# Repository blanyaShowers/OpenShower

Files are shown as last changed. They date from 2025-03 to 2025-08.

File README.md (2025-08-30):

# OpenShower: One Place for Sensations & Sophistication
OpenShower (OS) is a fully open, modular shower system designed to save water and energy — focused on delivering the best shower experience without the need to spend thousands of dollars or modify your bathroom installation. Thanks to its all-in-one, ready-to-use design, you can build it, customize it, and repair it yourself — driven by the vision that owning a premium shower should be as simple as buying a coffee machine.

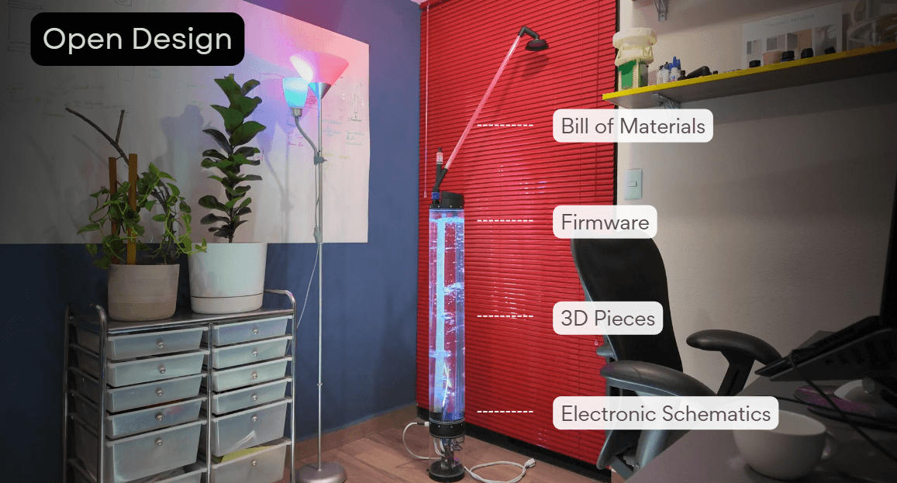
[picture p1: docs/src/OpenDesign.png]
os


OpenShower reinvents the shower experience by eliminating invisible waste and making each session more efficient and sustainable. With a 19-liter tank, it sets a natural water limit that encourages better habits without compromising comfort. The exact amount of water is preheated and delivered instantly, reducing waste during heat-up. Automatic pressure control eliminates the need for manual adjustments, saving time and optimizing water use. The transparent cylinder shows real-time water usage, while the top display reveals insights you’ve likely never seen before.

## Fusion 360:

The 3D model includes only the printable parts and their placement to help you identify each shower component. Acrylic pipes are shown for reference, but they are not intended to be printed.

Colored View: [https://a360.co/467mWWJ](https://a360.co/467mWWJ)

Black View: [https://a360.co/4nfyCwQ](https://a360.co/4nfyCwQ)

## Instructables:

Additional building details based on the YouTube video, plus extra insights about the process.

[https://www.instructables.com/OpenShower-One-Place-for-Sensations-Sophistication/](https://www.instructables.com/OpenShower-One-Place-for-Sensations-Sophistication/)

## Youtube:
The YouTube video walks through the 18 steps to build the model, showing in detail how parts are handled, which tools are used, and extra insights only visible through video.

[https://www.youtube.com/watch?v=CI9o5aMDqA0](https://www.youtube.com/watch?v=CI9o5aMDqA0)

## Kickstarter:
It’s time to break free from monotony, inefficiency, and the lack of innovation and new experiences in our showers. 

[https://www.kickstarter.com/projects/blanya/openshower-waste-ends-here?ref=24dbeq](https://www.kickstarter.com/projects/blanya/openshower-waste-ends-here?ref=24dbeq)

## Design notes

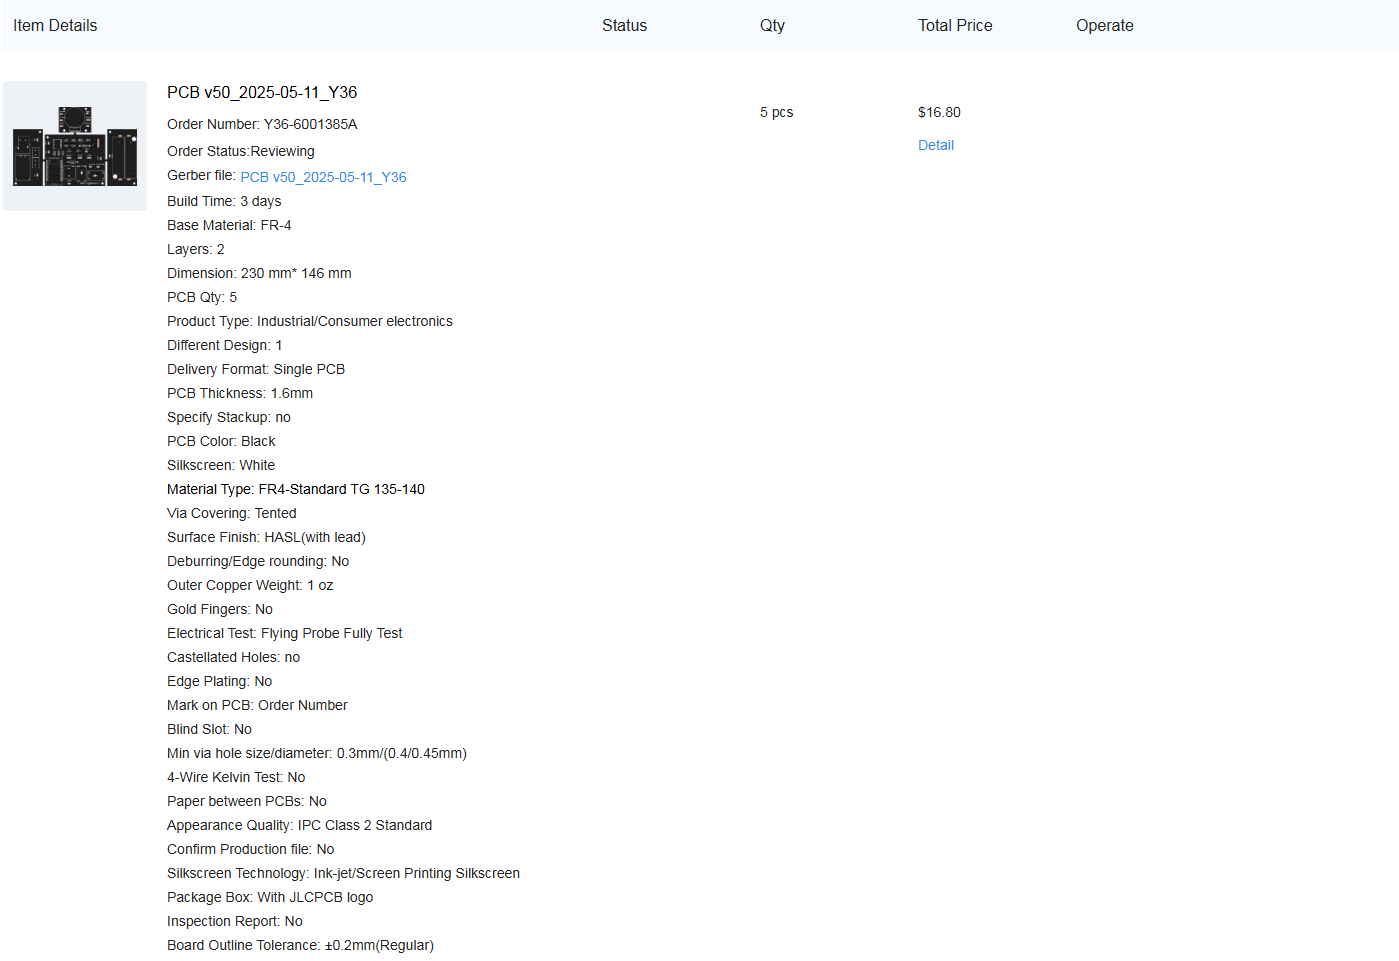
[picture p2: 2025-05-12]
hardware/electronics/ManufactoringDetails.png

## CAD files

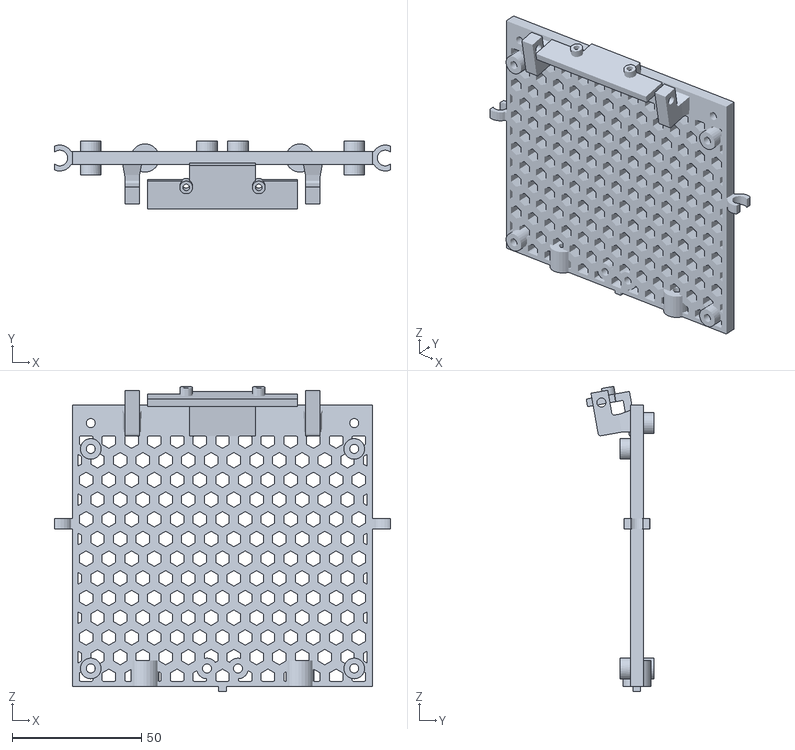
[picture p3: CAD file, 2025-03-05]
hardware/3dPieces/MainElectronicsSupport/MainElectronicSupport.stl
130.1 x 26.2 x 118.2

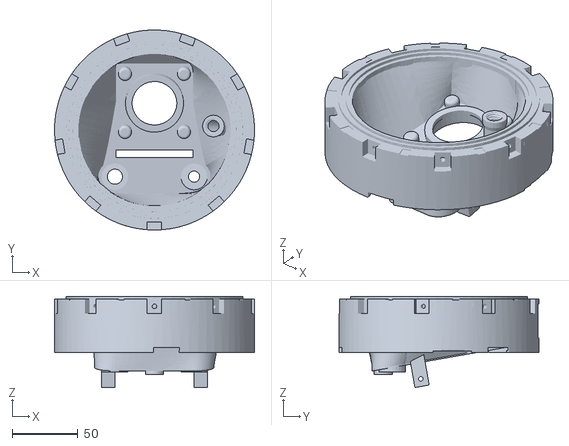
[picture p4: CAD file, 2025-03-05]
hardware/3dPieces/MainBottomSupport/Tank-MainSupport.stl
151.6 x 151.6 x 69.1

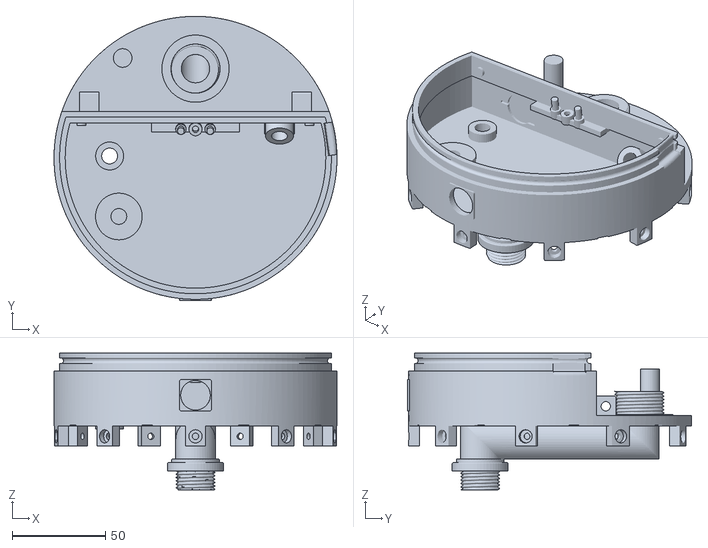
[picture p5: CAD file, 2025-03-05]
hardware/3dPieces/TopCap/MainTopSupport.stl
151.6 x 152.3 x 73.1

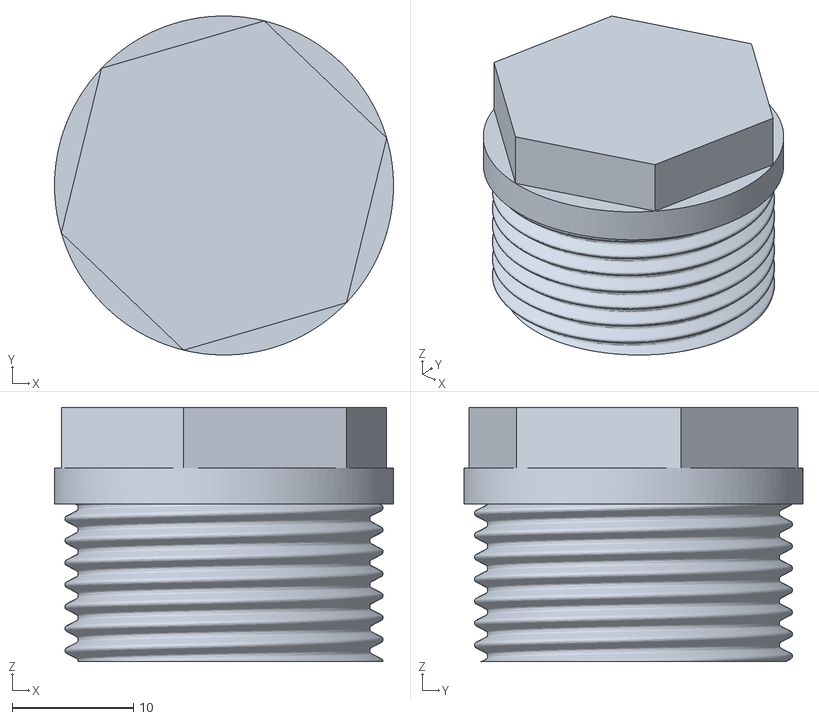
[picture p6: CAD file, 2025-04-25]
hardware/3dPieces/Accesories/ToSailWaterAdapter.stl
28.0 x 28.0 x 21.0

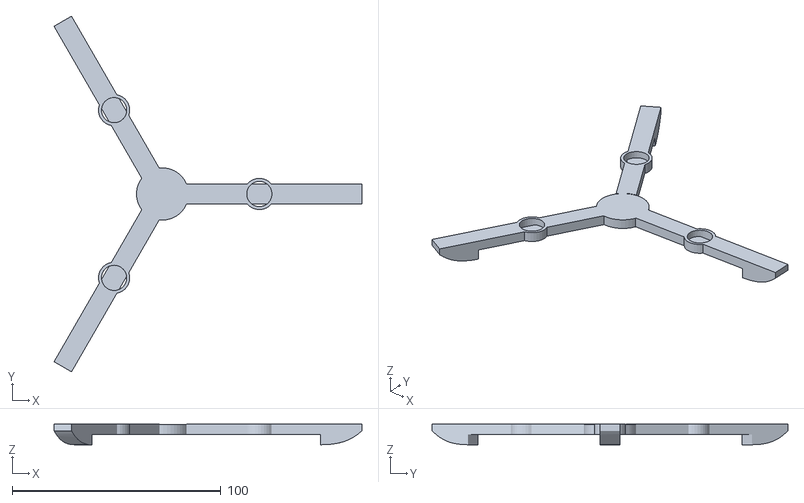
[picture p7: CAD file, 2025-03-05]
hardware/3dPieces/Base/Aditional-Support.stl
147.7 x 170.5 x 9.85

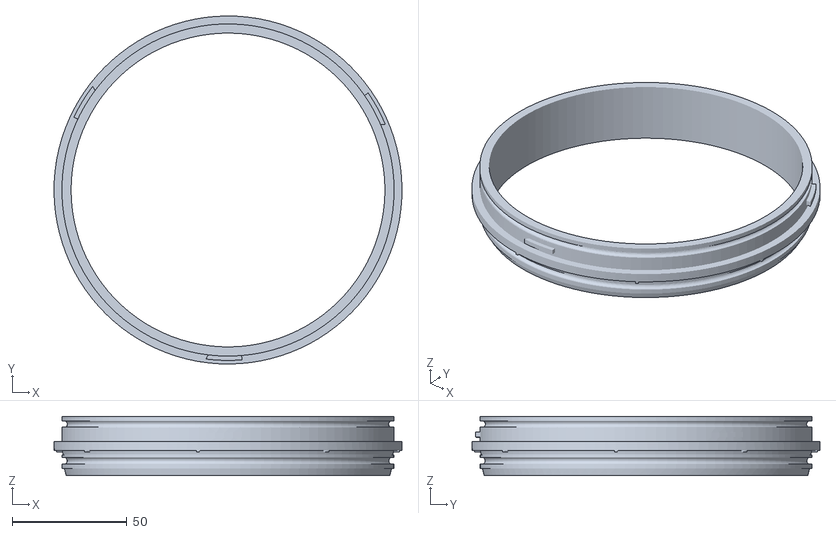
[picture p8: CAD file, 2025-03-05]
hardware/3dPieces/ElectronicsPipeAdapters/Bottom-ElectronicsAdapter-144-60.stl
151.6 x 151.6 x 25.7

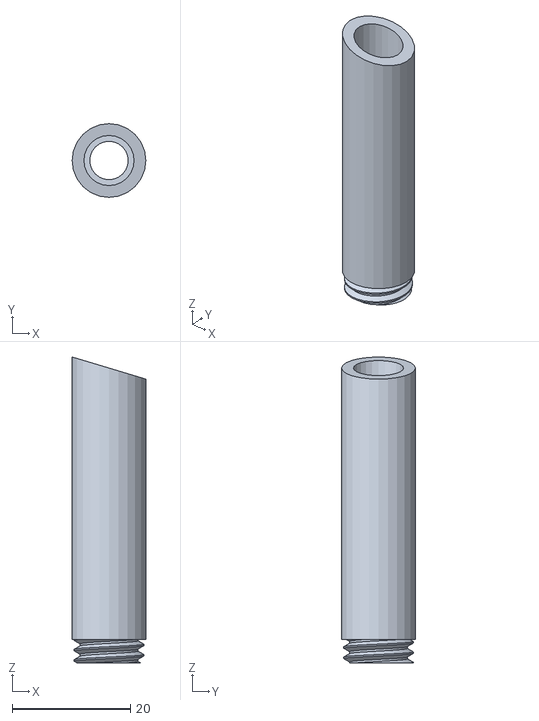
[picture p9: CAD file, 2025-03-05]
hardware/3dPieces/MainBottomSupport/Tank-AirOutput.stl
12.5 x 12.5 x 51.8

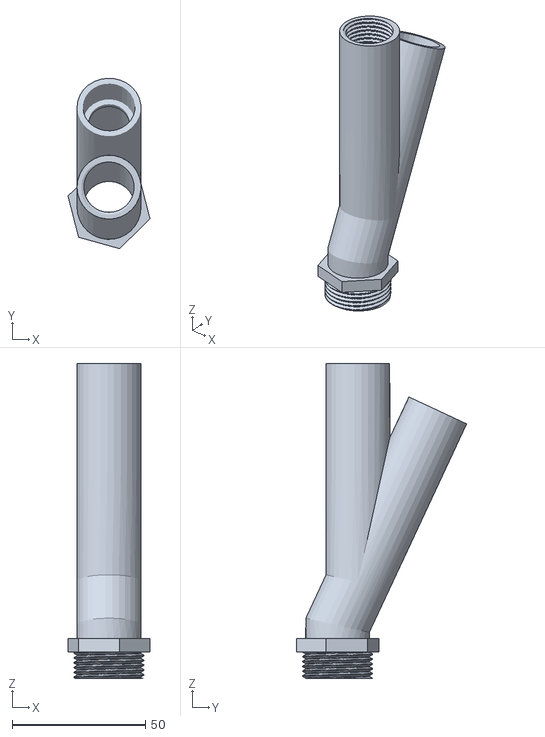
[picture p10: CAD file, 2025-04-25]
hardware/3dPieces/ShowerArm/Y.stl
30.8 x 64.0 x 118.3

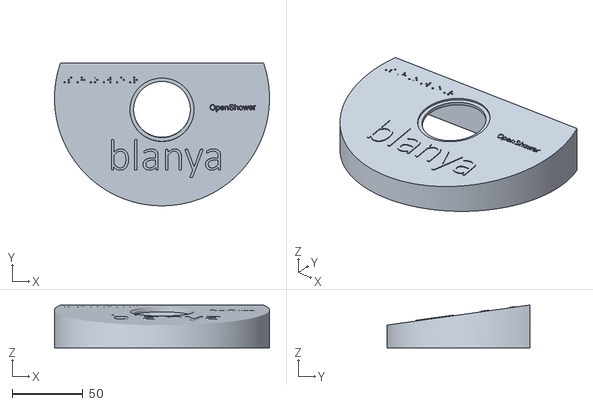
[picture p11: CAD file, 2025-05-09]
hardware/3dPieces/TopCap/ElectronicsCover.stl
151.6 x 100.6 x 30.0

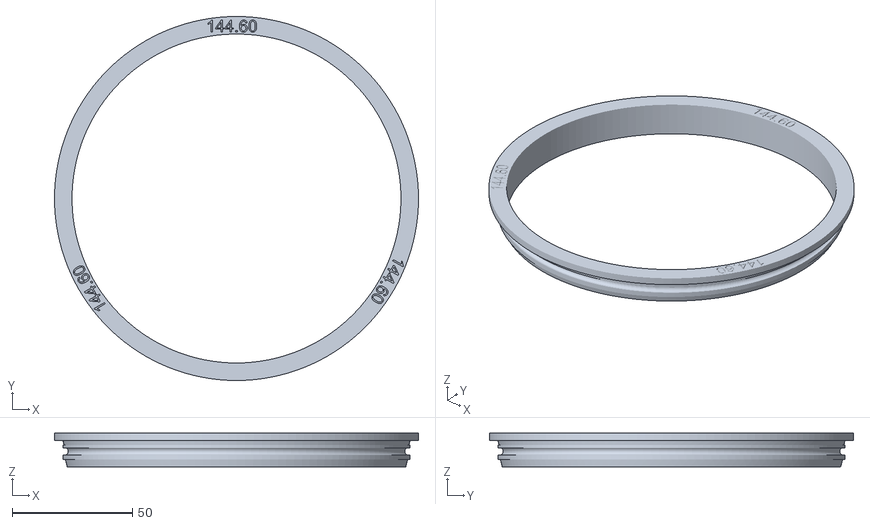
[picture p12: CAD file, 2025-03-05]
hardware/3dPieces/ToTestPipeDiameter/TankAdapter-OD-144-60.stl
151.6 x 151.6 x 14.0

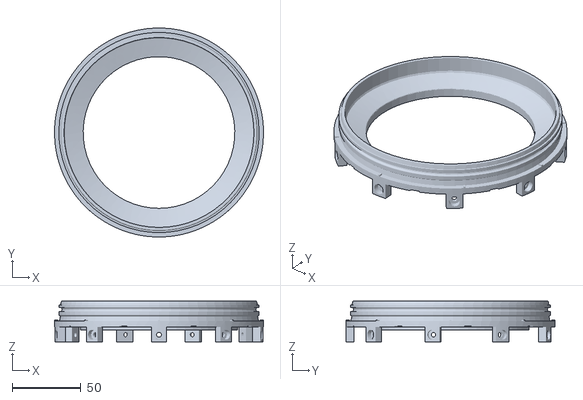
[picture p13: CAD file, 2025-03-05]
hardware/3dPieces/WaterPipeAdapters/Bottom-Adapter-145-20.stl
151.6 x 151.6 x 29.5

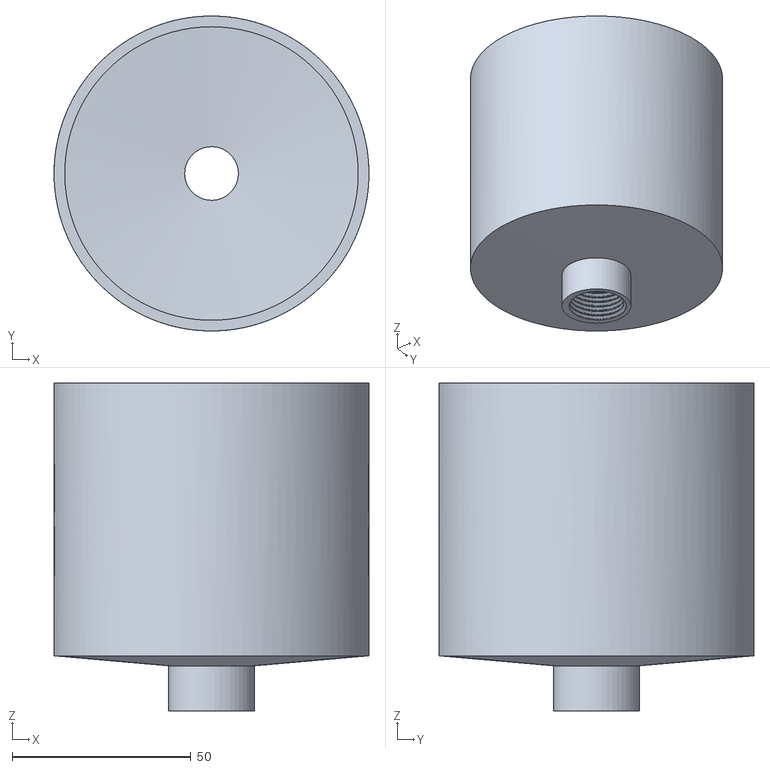
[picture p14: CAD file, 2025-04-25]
hardware/3dPieces/Accesories/Funel.stl
88.0 x 88.0 x 91.5

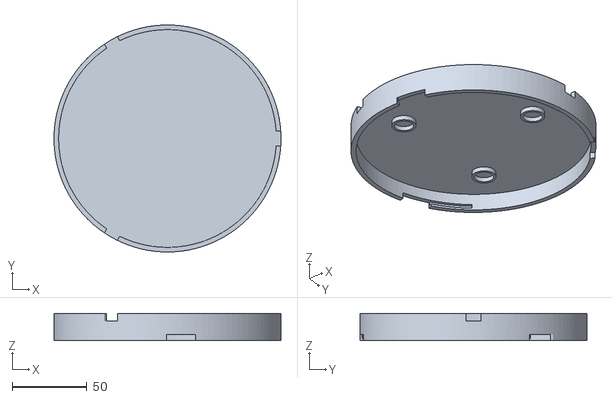
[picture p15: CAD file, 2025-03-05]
hardware/3dPieces/Base/Bottom-Cap.stl
151.6 x 151.6 x 18.1

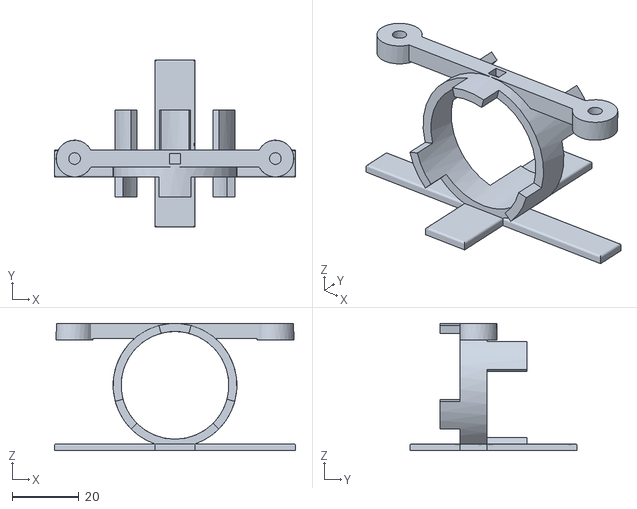
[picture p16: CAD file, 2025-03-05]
hardware/3dPieces/MainElectronicsSupport/MotorSupport.stl
72.0 x 50.0 x 38.0

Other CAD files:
hardware/3dPieces/ElectronicsPipeAdapters/Top-ElectronicsTopAdapter-144-60.stl
hardware/3dPieces/ShowerArm/Filter.stl
hardware/3dPieces/TopCap/CapSolenoid.stl
hardware/3dPieces/ToTestPipeDiameter/TankAdapter-OD-145-20.stl
hardware/3dPieces/MainBottomSupport/Tank-Window.stl
hardware/3dPieces/ShowerArm/ShowerHead-Part-1.stl
hardware/3dPieces/ShowerArm/ShowerHead-Part-2.stl
hardware/3dPieces/ShowerArm/TopAdapterShowerHead.stl
hardware/3dPieces/ToTestPipeDiameter/TankAdapter-OD-145-80.stl
hardware/3dPieces/TopCap/PipeAdapter.stl
hardware/3dPieces/TopCap/ScreenSupport-11mm.stl
hardware/3dPieces/TopCap/ScreenSupport.stl
hardware/3dPieces/TopCap/WaterIO.stl
hardware/3dPieces/WaterPipeAdapters/Top-TankAdapter-145-20.stl

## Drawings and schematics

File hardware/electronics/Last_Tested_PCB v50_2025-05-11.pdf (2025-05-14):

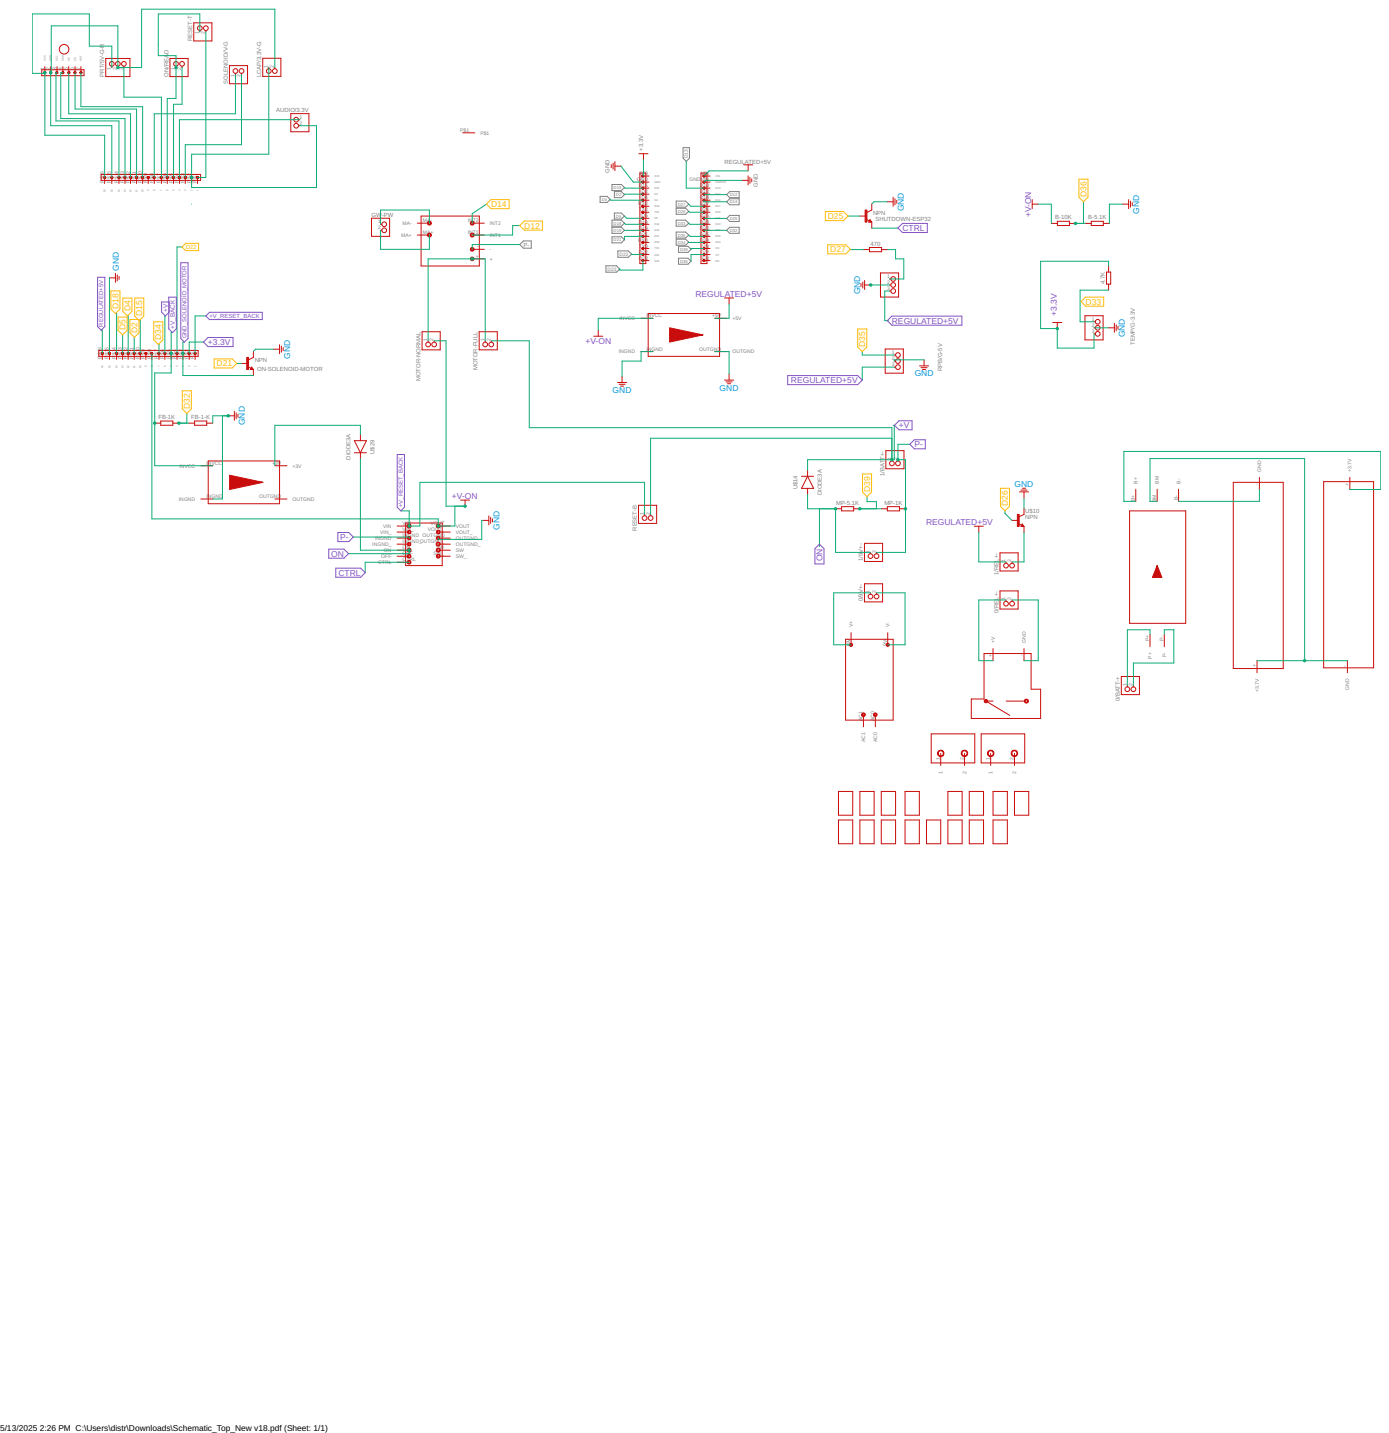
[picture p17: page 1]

5/13/2025 2:26 PM C:\Users\distr\Downloads\Schematic_Top_New v18.pdf (Sheet: 1/1)

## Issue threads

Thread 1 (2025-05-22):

Improve Battery Charging Speed to Ensure Optimal Performance

enerkup, 2025-05-22:
**Description:**
When the shower is connected to the main power, the batteries begin charging automatically. However, after 1–2 hours of charging, the battery level remains low.

**Problem:**
Slow charging results in incomplete battery cycles. When the battery is not fully charged, the motor does not run at optimal speed, leading to low water pressure.

**Suggested improvement:**
We need to increase the charging speed to ensure the battery reaches a sufficient level within a short period of connection time.

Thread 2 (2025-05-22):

Improved Battery Autonomy Needed to Maintain Quality of Use

enerkup, 2025-05-22:
**Description:**
Current battery autonomy supports approximately 10 continuous showers per full charge, which is acceptable. However, water pressure begins to drop around the 5th shower.

**Problem:**
This pressure drop indicates that the batteries may not sustain consistent power output throughout the entire cycle. With upcoming plans to integrate additional components like sensors, lights, or motors, the current 2× battery setup may not be sufficient.

**Suggested Improvement:**
Consider increasing the battery capacity or adding more batteries to ensure consistent water pressure and overall performance across all showers.

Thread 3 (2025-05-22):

Improve Battery Autonomy Needed to Maintain Quality of Use

enerkup, 2025-05-22:
**Description:**
Current battery autonomy supports approximately 10 continuous showers per full charge, which is acceptable. However, water pressure begins to drop around the 5th shower.

**Problem:**
This pressure drop indicates that the batteries may not sustain consistent power output throughout the entire cycle. With upcoming plans to integrate additional components like sensors, lights, or motors, the current 2× battery setup may not be sufficient.

**Suggested Improvement:**
Consider increasing the battery capacity or adding more batteries to ensure consistent water pressure and overall performance across all showers.

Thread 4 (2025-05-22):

Battery Level Readings Inaccurate

enerkup, 2025-05-22:
**Description:**
The current algorithm and resistor configuration do not accurately measure the real battery level, resulting in unreliable battery status information. Additionally, when the shower is connected to main power, it’s currently impossible to accurately read the battery level.

**Problem:**
Inaccurate battery readings can lead to incorrect user notifications about remaining battery life. Precise battery level monitoring is essential to enable new features, such as adjusting lighting or motor pressure dynamically.

**Suggested Improvement:**
Review and improve both the battery level sensing algorithm and the related electronics to ensure precise and reliable readings.

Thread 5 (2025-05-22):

Leak Issue in IP68 PG7 Cable Gland

enerkup, 2025-05-22:
**Description:**
The main power cable passes through the IP68 PG7 cable gland. During shower use, small water droplets sometimes fall onto the cable and penetrate into the electronic components. Even small amounts of water can accumulate and cause problems over time.

**Problem:**
Water intrusion is evidenced by condensation forming inside the lower tube, indicating moisture inside the electronics, which risks damage or failure.

**Suggested Improvement:**
Investigate and improve the sealing of the cable gland to prevent water ingress and protect electronic components from moisture.

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

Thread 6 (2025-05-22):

Leak and Interference in FCC Cable

enerkup, 2025-05-22:
**Description:**
The FCC cable that transmits data from the bottom to the top is wrapped with adhesive tape. However, when the tape reaches the upper cover, it is not fully sealed.

**Problem:**
During intensive shower use, water can gradually seep between the cable and the tape, causing moisture buildup and signal interference. This issue can be diagnosed when the display flickers or goes black.

**Suggested Improvement:**
Improve the sealing method around the FCC cable at the upper cover to prevent water ingress and ensure stable signal transmission.

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

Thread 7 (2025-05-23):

Replace Power Plug Male Adapter Cable for Better Water Isolation

enerkup, 2025-05-23:
**Description:**
The current power plug has a hole where the cable passes through, allowing potential water ingress. Its insulation is inadequate for wet environments.

**Problem:**
Water exposure risks electrical shorts or damage due to insufficient sealing.

**Suggested Improvement:**
Replace the existing connector with a fully sealed, water-resistant power plug designed specifically for humid or wet conditions to ensure safety and reliability.
Nominal voltage rating: 15 A, 125 VAC.

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

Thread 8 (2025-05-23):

Power Plug Male Adapter Cable – Improve Water Isolation

enerkup, 2025-05-23:
**Description:**
The current power plug has a hole where the cable passes through, which could allow water ingress. Its insulation is not optimal for wet environments. So far, it hasn’t caused problems, but it would be better to find a more suitable connector. Current connector rating: 15 A, 125 VAC.

**Problem:**
Exposure to water could lead to electrical shorts or long-term damage due to insufficient sealing.

**Suggested Improvement:**
Replace or improve the sealing of the current connector. Ideally, find a fully sealed plug designed for wet or humid conditions to ensure safety and reliability. So far, I haven’t found a better alternative.

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

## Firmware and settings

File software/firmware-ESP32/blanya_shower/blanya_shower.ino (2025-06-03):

#include <Arduino.h>
#include <SPI.h>
#include <TFT_eSPI.h>
#include <Sounds.h> 
#include <OneWire.h> 
#include <DallasTemperature.h> 
#include <Adafruit_NeoPixel.h>
#include <Preferences.h>
#include <lvgl.h>
#include "ui.h"

#include <FS.h>
#include <SPIFFS.h>
#include <ArduinoJson.h>

#include <BLEDevice.h>
#include <BLEUtils.h>
#include <BLEServer.h>


/* Other used Ports 
Check screen ports .\libraries\TFT_eSPI\User_Setups\Setup46_GC9A01_ESP32.h
*/

#define SERVICE_UUID        "4fafc201-1fb5-459e-8fcc-c5c9c331914b"
#define CHARACTERISTIC_UUID BLEUUID((uint16_t)0x2A1C)
#define CHARAC_UUID_SET_TEMPERATURE "e7810a71-73ae-499d-8c85-beb7aaedc10b"
#define CHARAC_UUID_SET_EXPERIENCE "9bca40c9-a1c4-4769-a52a-6412269d6f42"

BLEServer* pServer;
BLEService* pService;

BLECharacteristic* pCharCurrentTemp;
BLECharacteristic* pCharDesiredTemp;
BLECharacteristic* pCharDesiredExperience;

bool BTConnected = false;

const int MY_DISP_HOR_RES = 240;

/*Screen resolution*/
static const uint32_t screenWidth = 240;
static const uint32_t screenHeight = 240;
static lv_disp_draw_buf_t draw_buf;
static lv_color_t buf[screenWidth * 10];

#define MOTOR_PIN1 12
#define MOTOR_PIN2 14

#define ReadBatteryPower 36
#define ReadMainPower 39
#define ReadPressureTop 34
#define ReadPressureBottom 35
#define ReadMainButton 32
#define ReadTemperature 33  

#define PWMSound 22
#define TransOnSolenoidMotor 21
#define ShutdownESP32 25  
#define TransOnHeatElement 26
#define NeopixelOut 27        

#define NUMPIXELS 8

float DesiredTemperature;
String ShowerExperience;
bool PendingToShutdown = false;
bool Battery = false;
bool MainPower = false;
double TemperatureCelsius = 0;
bool Play = false;
bool ErrorReadingTemperature = false;
double rMainPower = 0;

bool unique = true;
int BatteryReadings [6] = {0,0,0,0,0,0};
int readIndex = 0;
int motorSpeed = 0;
int motorSpeedMP = 0;
int totalReadingsBattery = 0;
double averageBatteryReading = 0;

int pressure2Readings [6] = {0,0,0,0,0,0};
int totalReadingPressure2 = 0;
double averagePressureBottom = 0;

int mainPowerReadings [6] = {0,0,0,0,0,0};
int readIndexMainPower = 0;
int totalReadingsMainPower = 0;
double averageMainPowerReading = 0;

int firstClick = 0;
int currentIndex = 0;


DynamicJsonDocument doc(1224); // Adjust capacity as needed

// Setup a oneWire instance to communicate with any OneWire devices (not just Maxim/Dallas temperature ICs)
OneWire oneWire(ReadTemperature);
DallasTemperature temperatureSensor(&oneWire);

TFT_eSPI tft = TFT_eSPI();

Sounds UserSounds = Sounds(PWMSound);

Adafruit_NeoPixel pixels(NUMPIXELS, NeopixelOut, NEO_GRB + NEO_KHZ800);

Preferences preferences;

static lv_obj_t * ta;

void loop2(void * pvParameters);

void ShowerPlanner();

void PixelsLight(int arr[3])
{
  pixels.clear(); // Set all pixel colors to 'off'
  pixels.fill(pixels.Color(arr[0],arr[1],arr[2]));
  pixels.setBrightness(255);
  pixels.show(); // Send the updated pixel colors to the hardware.

}

void PixelsLight(int intensity, int arr[3])
{
  pixels.clear(); // Set all pixel colors to 'off'
  pixels.fill(pixels.Color(arr[0],arr[1],arr[2]));
  pixels.setBrightness(intensity);
  pixels.show(); // Send the updated pixel colors to the hardware.

}

void PixelsWelcome()
{

  // The first NeoPixel in a strand is #0, second is 1, all the way up
  // to the count of pixels minus one.
  
  pixels.clear(); // Set all pixel colors to 'off'

  pixels.setPixelColor(0, pixels.Color(255, 182, 193)); // Rosa claro
  pixels.setPixelColor(1, pixels.Color(255, 182, 193)); // Rosa claro
  pixels.setPixelColor(2, pixels.Color(255, 182, 193)); // Rosa claro
  
  pixels.setPixelColor(3, pixels.Color(173, 216, 230)); // Azul claro
  pixels.setPixelColor(4, pixels.Color(173, 216, 230)); // Azul claro
  
  pixels.setPixelColor(5, pixels.Color(240, 230, 140)); // Amarillo pálido
  pixels.setPixelColor(6, pixels.Color(240, 230, 140)); // Amarillo pálido
  pixels.setPixelColor(7, pixels.Color(240, 230, 140)); // Amarillo pálido

  pixels.show(); // Send the updated pixel colors to the hardware.

}

/* Display flushing */
void my_disp_flush( lv_disp_drv_t *disp, const lv_area_t *area, lv_color_t *color_p )
{
    uint32_t w = ( area->x2 - area->x1 + 1 );
    uint32_t h = ( area->y2 - area->y1 + 1 );

    tft.startWrite();
    tft.setAddrWindow( area->x1, area->y1, w, h );
    tft.pushColors( ( uint16_t * )&color_p->full, w * h, true );
    tft.endWrite();

    lv_disp_flush_ready( disp );
}

void airPumpIn(int value){
  analogWrite(MOTOR_PIN1, value); 
}

void initiateShutdown() {
    UserSounds.Shutdown();
    digitalWrite(ShutdownESP32, HIGH);
    Play = false;
    airPumpIn(0);
    delay(10000);
}

class MyServerCallbacks: public BLEServerCallbacks {
    void onConnect(BLEServer* pServer) { BTConnected = true; }
    void onDisconnect(BLEServer* pServer) { 
        BTConnected = false; 
        pServer->startAdvertising(); // Restart advertising on disconnect
    }
};


bool indicationAcknowledged = false;

class MyCharacteristicCallbacks : public BLECharacteristicCallbacks {

  void onWrite(BLECharacteristic *pCharacteristic) {
        std::string value = pCharacteristic->getValue(); // Get the written value as a string
        if (value.length() > 0) {
            // Check which characteristic was written to
            if (pCharacteristic == pCharDesiredTemp) {
                // Characteristic 1: Temperature threshold (float, 4 bytes)
                try {
                    float tempFromUser = std::stof(value);
                    if(tempFromUser > 45 || tempFromUser <= 0.0f) {
                        Serial.printf("Error: Invalid temperature %.1f\n", tempFromUser);
                        UserSounds.Error();
                        return;
                    }
                    
                    preferences.begin("blanya-settings", false);
                    preferences.putFloat("max_temp", tempFromUser);
                    DesiredTemperature = tempFromUser;
                    preferences.end();
                    UserSounds.BluetoothNewPreference();
                }
                catch (const std::exception& e) {
                    Serial.printf("Error parsing temperature: %s\n", e.what());
                    UserSounds.Error();
                } 
            }   
            else if (pCharacteristic == pCharDesiredExperience) {

                switch (std::stoi(value)) {
                  case 1:
                    preferences.begin("blanya-settings", false);
                    preferences.putString("experience", "p1-PourOver");
                    preferences.end();
                    UserSounds.BluetoothNewPreference();
                    ESP.restart();
                    break;
                    
                  case 2:
                    preferences.begin("blanya-settings", false);
                    preferences.putString("experience", "p2-Barista");
                    preferences.end();
                    UserSounds.BluetoothNewPreference();
                    ESP.restart();
                    break;

                  case 3:
                    preferences.begin("blanya-settings", false);
                    preferences.putString("experience", "p3-Infusion");
                    preferences.end();
                    UserSounds.BluetoothNewPreference();
                    ESP.restart();
                    break;
              
                  default:
                    preferences.begin("blanya-settings", false);
                    preferences.putString("experience", "p0-Default");
                    preferences.end();
                    UserSounds.BluetoothNewPreference();
                    ESP.restart();
                    break;
                }
            }          
        }
    } 
};


void setup()
{

  Serial.begin(115200);
  
  pinMode(TransOnHeatElement, OUTPUT);
  pinMode(ShutdownESP32, OUTPUT);
  pinMode(TransOnSolenoidMotor, OUTPUT);
  
  analogWrite(MOTOR_PIN1, 0);
  analogWrite(MOTOR_PIN2, 0);
      
  tft.init();
  tft.setRotation(0);
  tft.fillScreen(TFT_LIGHTGREY);
  tft.textbgcolor = TFT_LIGHTGREY;
  tft.textcolor = TFT_BLACK;

  tft.drawString("blanya", 82, 100, 4);

  lv_init();

  delay(1000);

  /*Initialize `disp_buf` with the buffer(s). With only one buffer use NULL instead buf_2 */
  lv_disp_draw_buf_init(&draw_buf, buf, NULL, screenWidth * 10);

  /*Initialize the display*/
  static lv_disp_drv_t disp_drv;
  lv_disp_drv_init(&disp_drv);

  disp_drv.hor_res = screenWidth;
  disp_drv.ver_res = screenHeight;
  disp_drv.flush_cb = my_disp_flush;
  disp_drv.draw_buf = &draw_buf;
  lv_disp_drv_register(&disp_drv);

  ui_init();

  temperatureSensor.begin();

  pixels.begin();
  PixelsWelcome();

  preferences.begin("blanya-settings", false);
  DesiredTemperature = preferences.getFloat("max_temp",30.00);
  ShowerExperience = preferences.getString("experience","default");
  preferences.end();

  xTaskCreatePinnedToCore (
    loop2,     // Function to implement the task
    "loop2",   // Name of the task
    12500,      // Stack size in bytes
    NULL,      // Task input parameter
    0,         // Priority of the task
    NULL,      // Task handle.
    0          // Core where the task should run
  );
  
  UserSounds.Start();

  BLEDevice::init("Blanya OS V1.0");
  pServer = BLEDevice::createServer();
  pServer->setCallbacks(new MyServerCallbacks());
  
  pService = pServer->createService(SERVICE_UUID);
  
  pCharCurrentTemp = pService->createCharacteristic(
      CHARACTERISTIC_UUID,
      BLECharacteristic::PROPERTY_NOTIFY 
  ); 

  BLEDescriptor *pCCCD = new BLEDescriptor(BLEUUID((uint16_t)0x2902));
  pCharCurrentTemp->addDescriptor(pCCCD);
  
  pCharDesiredTemp = pService->createCharacteristic(
      CHARAC_UUID_SET_TEMPERATURE,
      BLECharacteristic::PROPERTY_READ |
      BLECharacteristic::PROPERTY_WRITE |
      BLECharacteristic::PROPERTY_NOTIFY |
      BLECharacteristic::PROPERTY_INDICATE
  ); 

  pCharDesiredExperience = pService->createCharacteristic(
      CHARAC_UUID_SET_EXPERIENCE,
      BLECharacteristic::PROPERTY_READ |
      BLECharacteristic::PROPERTY_WRITE |
      BLECharacteristic::PROPERTY_NOTIFY |
      BLECharacteristic::PROPERTY_INDICATE
  ); 

  MyCharacteristicCallbacks* callbacks = new MyCharacteristicCallbacks();
  pCharDesiredTemp->setCallbacks(callbacks);
  pCharDesiredExperience->setCallbacks(callbacks);

  pService->start();
  
  BLEAdvertising* pAdvertising = pServer->getAdvertising();
  pAdvertising->start();
  Serial.println("BLE Ready!");

  if (!SPIFFS.begin(true)) { 
    Serial.println("Failed to mount SPIFFS");
    return;
  }

  fs::File file = SPIFFS.open("/"+ShowerExperience+".json", FILE_READ);
  if (!file) {
    Serial.println("Failed to open .json");
    return;
  }

  // Read file into String (workaround if file.size() fails)
  String jsonContent = file.readString();
  file.close();

  Serial.println("File contents:");
  Serial.println(jsonContent);

  // Parse JSON from String
  DeserializationError error = deserializeJson(doc, jsonContent);
  if (error) {
    Serial.print("deserializeJson() failed: ");
    Serial.println(error.c_str());
    return;
  }

  Serial.println("JSON file loaded successfully");

  firstClick = 0;
}


void loop()
{
    if (BTConnected) {

      uint8_t flags = 0x00; // Celsius, no timestamp, no type
      int32_t mantissa = (int32_t)(TemperatureCelsius * 1000); // Convert to milli-degrees
      uint8_t exponent = 0xFD; // Exponent -3 (10^-3)
      uint8_t value[5] = {
          flags,
          (uint8_t)(mantissa & 0xFF),
          (uint8_t)((mantissa >> 8) & 0xFF),
          (uint8_t)((mantissa >> 16) & 0xFF),
          exponent
      };
    
      pCharCurrentTemp->setValue(value,5); 
      pCharCurrentTemp->notify(); 

    } 

    temperatureSensor.requestTemperatures();
    if (TemperatureCelsius != DEVICE_DISCONNECTED_C)
    {
      TemperatureCelsius = temperatureSensor.getTempCByIndex(0);
      ErrorReadingTemperature = false; 
    }
    else {
      ErrorReadingTemperature = true; 
    }
  
    rMainPower = analogRead(ReadMainPower);
    totalReadingsMainPower -= mainPowerReadings[readIndexMainPower];
    mainPowerReadings[readIndexMainPower] = rMainPower;
    totalReadingsMainPower += rMainPower;
    averageMainPowerReading = totalReadingsMainPower / 6;  
    readIndexMainPower = (readIndexMainPower +1) % 6;
    
    if (averageMainPowerReading > 800)
    {
      MainPower = true;
      Battery = false;
      PendingToShutdown = true;
    }
    else
    {
      MainPower = false;
      Battery = true;
    }
}

void loop2(void * pvParameters)
{
  for( ;; )
  {

    lv_timer_handler();
    
    if(analogRead(ReadMainButton) > 1000) {
    UserSounds.OneClick();
    firstClick ++;
      if(unique) {
        if(Play) {
          Play = false;
          lv_obj_clear_flag(ui_batterylevel,LV_OBJ_FLAG_HIDDEN);
        } else {
          lv_obj_add_flag(ui_batterylevel,LV_OBJ_FLAG_HIDDEN);
          Play = true;
        }
        delay(800);
        if(analogRead(ReadMainButton) > 1000){
          delay(1000);
          if(analogRead(ReadMainButton) > 1000){
            PendingToShutdown = true;
          }
        }
      }
      unique = false;
    }
    else {      
      ShowerPlanner();
      unique = true;
    }

    int batteryLevel = analogRead(ReadBatteryPower);
    //double pTop = analogRead(ReadPressureTop);
    double pBottom = analogRead(ReadPressureBottom);

    totalReadingsBattery -= BatteryReadings[readIndex];
    BatteryReadings[readIndex] = batteryLevel;
    totalReadingsBattery += batteryLevel;

    averageBatteryReading = totalReadingsBattery / 6;  
    double batteryPercentage = ((averageBatteryReading - 2200) * 100) / (2750 - 2200); 

    totalReadingPressure2 -= pressure2Readings[readIndex];
    pressure2Readings[readIndex] = pBottom;
    totalReadingPressure2 += pBottom;
    averagePressureBottom = totalReadingPressure2 / 6;  

    readIndex = (readIndex +1) % 6;

    lv_label_set_text(ui_NumTemperature, ErrorReadingTemperature ? "ERT" : String(TemperatureCelsius, 1).c_str());    
    lv_label_set_text(ui_NumUserTemp, String(DesiredTemperature, 1).c_str());
    lv_label_set_text(ui_NumPressureBottom, String(averagePressureBottom, 0).c_str());
    lv_label_set_text(ui_batterylevel, (String(batteryPercentage, 0) + "%").c_str());

    if (BTConnected) {
      lv_obj_add_flag(ui_searching,LV_OBJ_FLAG_HIDDEN);
      lv_obj_clear_flag(ui_connected,LV_OBJ_FLAG_HIDDEN);
    }
    else {
      lv_obj_clear_flag(ui_searching,LV_OBJ_FLAG_HIDDEN);
      lv_obj_add_flag(ui_connected,LV_OBJ_FLAG_HIDDEN);  
      }

    lv_label_set_text(ui_ButtonStart, Play ? "Pause" : "Play");
          
    if(MainPower){
        lv_img_set_src(ui_default, &ui_img_electric_png);
      }

     if(Battery){
        if(ShowerExperience == "p1-PourOver"){
          lv_img_set_src(ui_default, &ui_img_pourover_png); //set icon theme 
        } else if (ShowerExperience == "p2-Barista"){
          lv_img_set_src(ui_default, &ui_img_barista_png); 
        } else if (ShowerExperience == "p3-Infusion"){
          lv_img_set_src(ui_default, &ui_img_tea_png); 
        } else if (ShowerExperience == "p0-Default") {
          lv_img_set_src(ui_default, &ui_img_default_png); 
          }  
      }
            
    
    vTaskDelay(5);

  }
}

void ShowerPlanner()
{
  
    unsigned long currentMillis = millis(); // Get time  

    if(PendingToShutdown && Battery) {
      initiateShutdown();
    }
    
    if(MainPower){

    static unsigned long previousMillis = 0;
    const unsigned long interval = 2000; 
  
    if (currentMillis - previousMillis >= interval) {
      previousMillis = currentMillis;
  
      unsigned long seconds = currentMillis / 2000;
      int color[] = {255, 100, 0};
          
      if (seconds % 2 == 0) {
        PixelsLight(255,color);
        motorSpeedMP = 255;
      } else {
        PixelsLight(200,color);
        motorSpeedMP = 200;
      }
      
    }

     digitalWrite(TransOnSolenoidMotor, LOW); // To avoid pressure accumulation
          
     if (TemperatureCelsius > DesiredTemperature)
        {
          digitalWrite(TransOnHeatElement, LOW); // Shutdown relay
          UserSounds.TemperatureReached();  // Alert the user that the water is ready     
          Play = false;
        }

      if(Play && averagePressureBottom > 10){
          digitalWrite(TransOnHeatElement, HIGH); // Start relay, heat water.
          airPumpIn(motorSpeedMP);
      }
      else {
          digitalWrite(TransOnHeatElement, LOW); // Stop relay.
          airPumpIn(0);
        }
        
    }

    
    if(Battery){

     digitalWrite(TransOnHeatElement, LOW); // Shutdown relay
     if(firstClick >= 1){
        digitalWrite(TransOnSolenoidMotor, HIGH); // Pressure accumulation
     }
      if(Play){
         airPumpIn(motorSpeed);
      }
      else {
         airPumpIn(0);
         
         // Implement security to avoid pressure accumulation if the user fills the tank when it is in use
        }


    JsonArray dataArray = doc["data"];
    if (dataArray.size() > 0 && currentIndex < dataArray.size()) {
        JsonObject item = dataArray[currentIndex];
        int duration = item["time"];

        static unsigned long itemStartTime = 0;
        static bool NextRun = true; 
    
        if (NextRun) {
            itemStartTime = currentMillis; // Save time
            NextRun = false;
            JsonArray lightColor = item["lc"];
            int colors[3] = {lightColor[1], lightColor[2], lightColor[3]};
            motorSpeed = item["power"];
            PixelsLight(lightColor[0],colors);
            Serial.println(itemStartTime); 
        }
    
        // Verify Time
        if (currentMillis - itemStartTime >= (unsigned long)duration) {
            currentIndex++;
            NextRun = true; // Next element
        }
      }
    }



    if(ErrorReadingTemperature == true){
      UserSounds.Error();
      Play = false; 
    }

}

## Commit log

2024-12-28 To change UI and remove lvgl examples
    Changes on UI and logic to read sensors values
2025-02-28 To avoid delay() in code
    Issue with delay(200) in screen synchronization and other performance changes.
    [blanya_shower.ino]
2025-03-05 3D Pieces and last Electronics Gerber Doc
    Pieces from the last version
    [1-Bottom-ElectronicsAdapter.stl, 1-ShowerArm-TopAdapter.stl, 1-Tank-Adapter-145-20.stl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]
2025-03-11 Change Bluetooth to BLE & Sounds improvements
    Commands to update the temperature and shutdown via BLE and sounds improvements
2025-04-02 UI Changes and Temperature BT
2025-04-08 Move ShowerPlanner responsibilities
    To print values on screen in loop2
2025-04-25 3D Pieces Update
    New pieces and folder structure
    [4-ShowerArm-KarcherAdapter.stl, Aditional-Support.stl, Bottom-Adapter-145-20.stl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]
2025-05-09 3D Pieces
    New structure
    [BOL.xlsx, ElectronicsCover.stl, Funel.stl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]
2025-05-10 Update Name of File and Content
    [BOL.xlsx]
2025-05-12 BOM Update and new Electronics versions
2025-05-14 Updated BOM and Schematics
2025-05-27 New Base Shower Profiles and PCB
    Tested last PCB design with battery performance improvements
